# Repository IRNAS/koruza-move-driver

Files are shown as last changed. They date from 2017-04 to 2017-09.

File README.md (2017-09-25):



# Koruza move driver

The Koruza driver is an additional board to [Koruza CM board][link1_koruza_compute_module_repo]. The Koruza move driver is just a simple board dedicated to only one true real-time task - moving the stepper motors.

The main and only MCU on the board is the one and only ATmega328P, which is Arduino compatible. The MCU tasks are: driving the stepper motors, reading the switches and encoders, and communicating with the main board. For driving motors, there is one high-current Darlington transistor array. On the board back, at the end of the motor shafts two magnetic encoders are positioned. Two encoders are TLV493D from Infineon.

For more information about the design of the koruza move driver please see the [Schematics and PCB design files in PDF format][link3_pdf].
The firmware for the koruza move driver board is in the [firmware repository][link2_fw_repo].

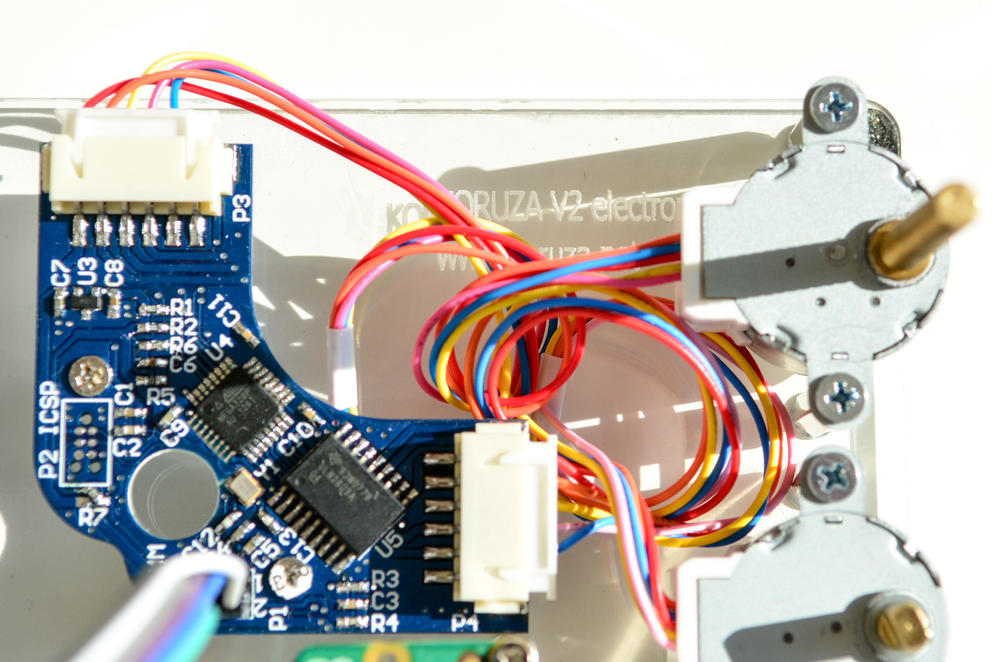
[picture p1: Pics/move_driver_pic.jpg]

---

## Licensing

KORUZA Pro Hardware with documentation, including Koruza move driver, is licensed under [CERN OHL v.1.2. license](https://www.ohwr.org/licenses/cern-ohl/license_versions/v1.2).

What this means is that you can use this hardware and documentation without paying a royalty and knowing that you'll be able to use your version forever. You are also free to make changes but if you share these changes then you have to do so on the same conditions that you enjoy.

KORUZA, KORUZA Pro and IRNAS are all names and marks of Institute IRNAS Rače. You may use these names and terms only to attribute the appropriate entity as required by the Open Licence referred to above. You may not use them in any other way and in particular you may not use them to imply endorsement or authorization of any hardware that you design, make or sell.

[link1_koruza_compute_module_repo]: https://github.com/IRNAS/koruza-compute-module
[link2_fw_repo]: https://github.com/IRNAS/Koruza-Move-Driver-Firmware
[link3_pdf]: https://github.com/IRNAS/koruza-move-driver/blob/master/Koruza%20move%20driver/Project%20Outputs%20for%20PCB_Project_KoruzaMoveDriver/koruza-move-driver-PCB.pdf

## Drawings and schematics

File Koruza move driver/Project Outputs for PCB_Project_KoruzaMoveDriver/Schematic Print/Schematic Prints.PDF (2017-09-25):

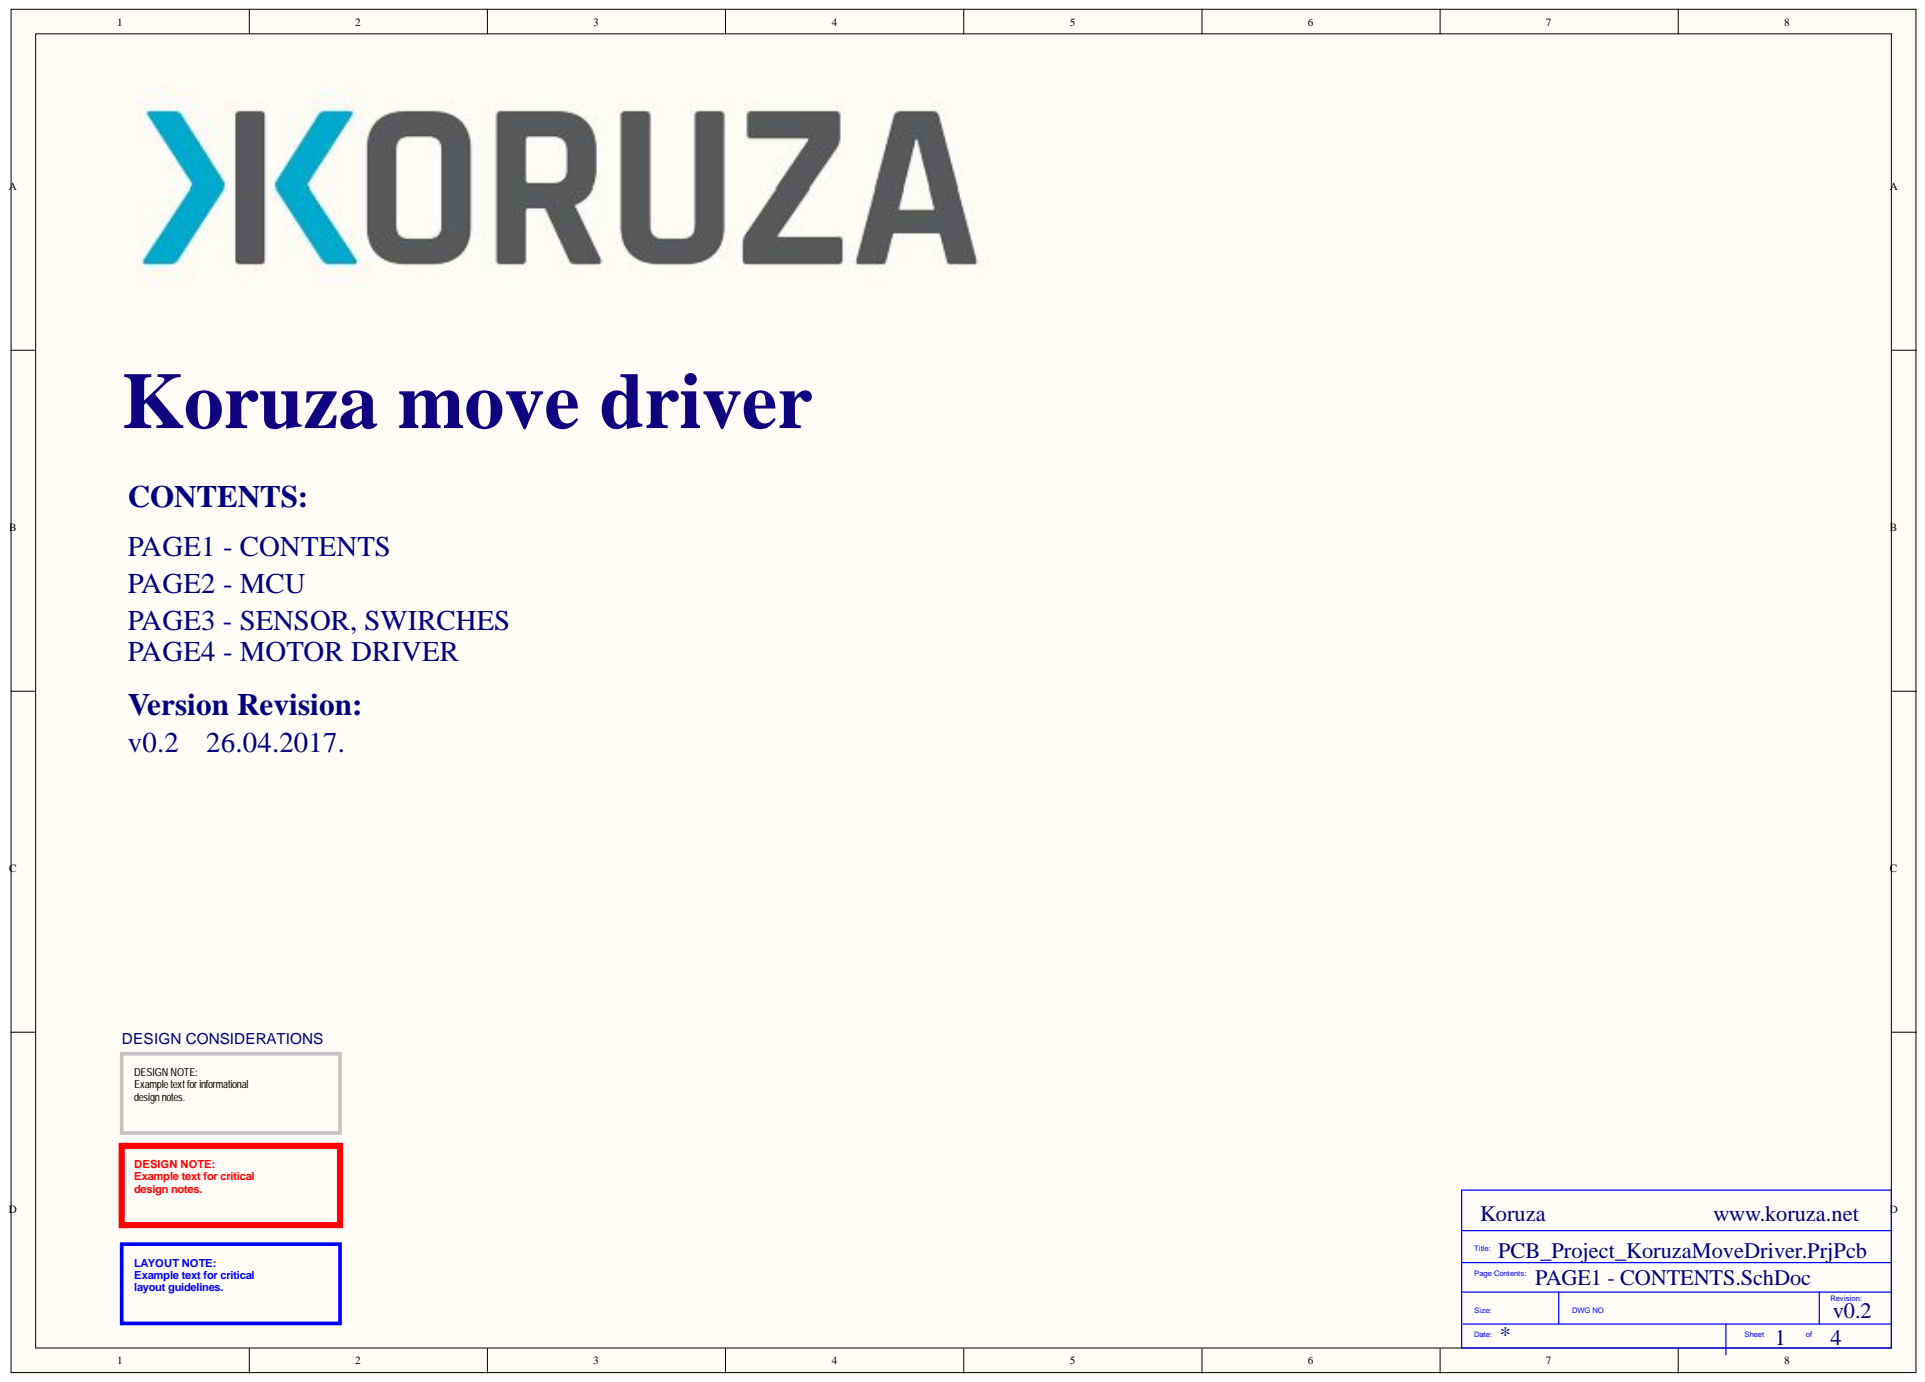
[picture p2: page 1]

DESIGN NOTE:
Example text for informational
design notes.

Example text for critical

LAYOUT NOTE:
layout guidelines.

Size: | DWG NO | Revision: v0.2

* Date: | 1 4 Sheet of

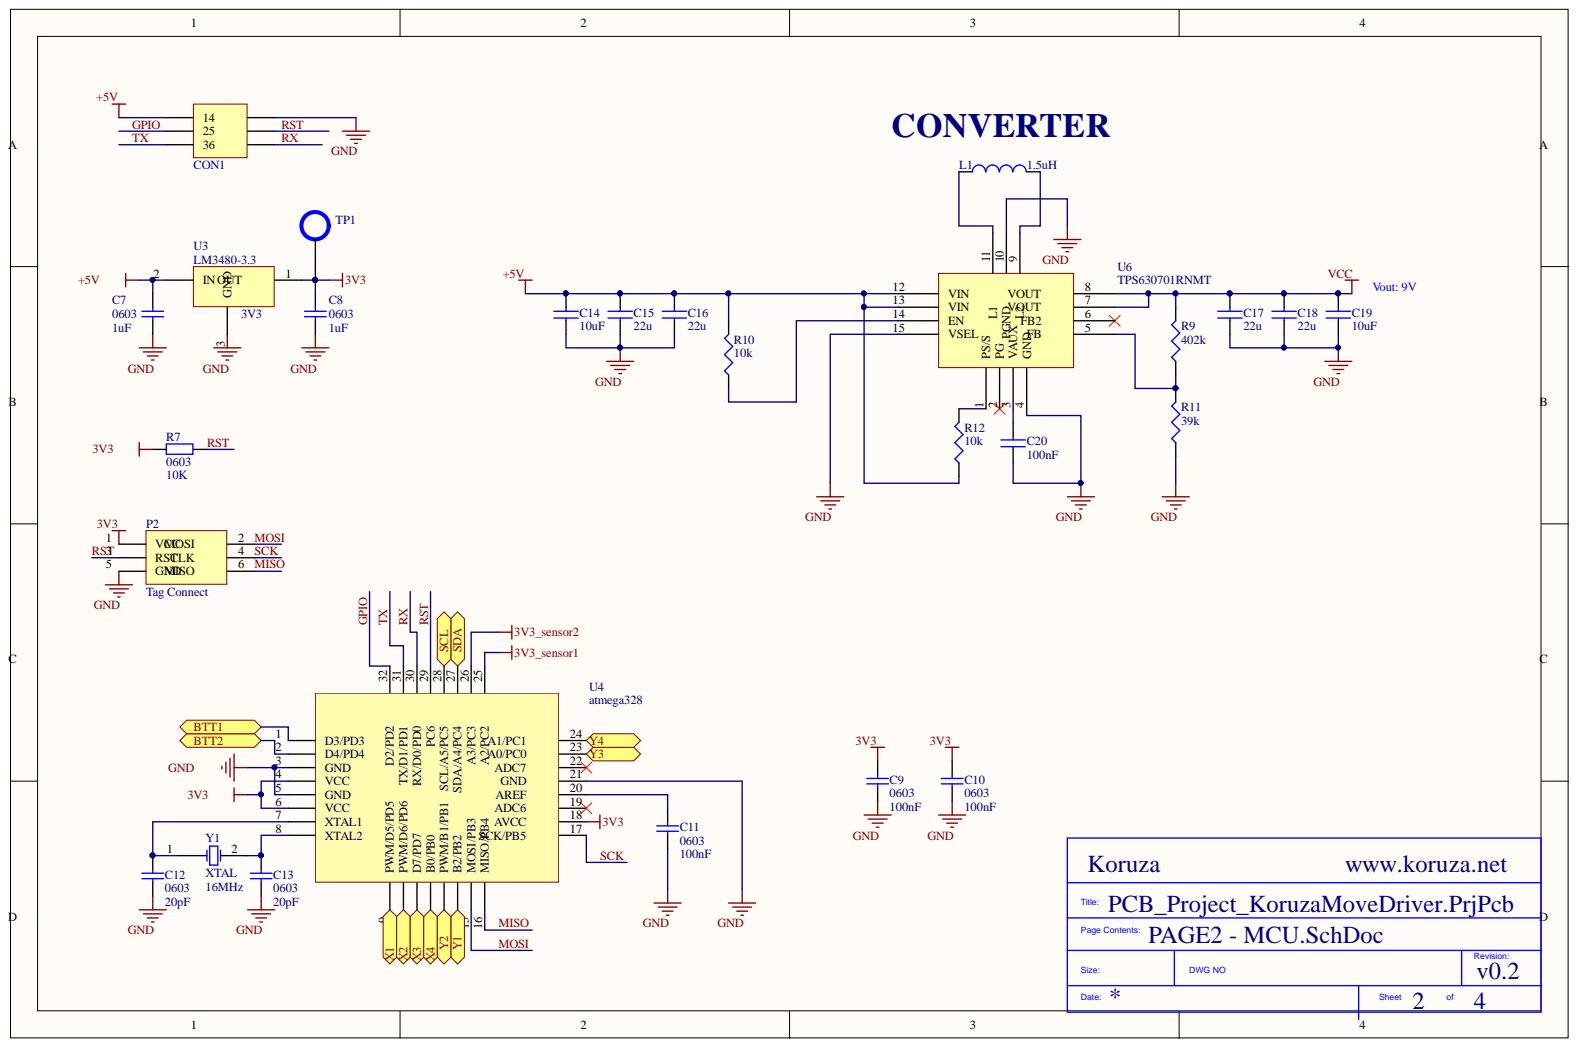
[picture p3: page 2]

GND 4 FB 5 FB2 6 VOUT 7 VOUT 8

A2/PC2 25 A3/PC3 26 SDA/A4/PC4 27 SCL/A5/PC5 28 PC6 29 RX/D0/PD0 30 TX/D1/PD1 31 D2/PD2 32

MISO/PB4 16 SCK/PB5 17 AVCC 18 ADC6 19 AREF 20 GND 21 ADC7 22 A0/PC0 23 A1/PC1 24

D4/PD4 2
GND 3

GND 5

Size: | DWG NO | Revision: v0.2

* Date: | 2 4 Sheet of

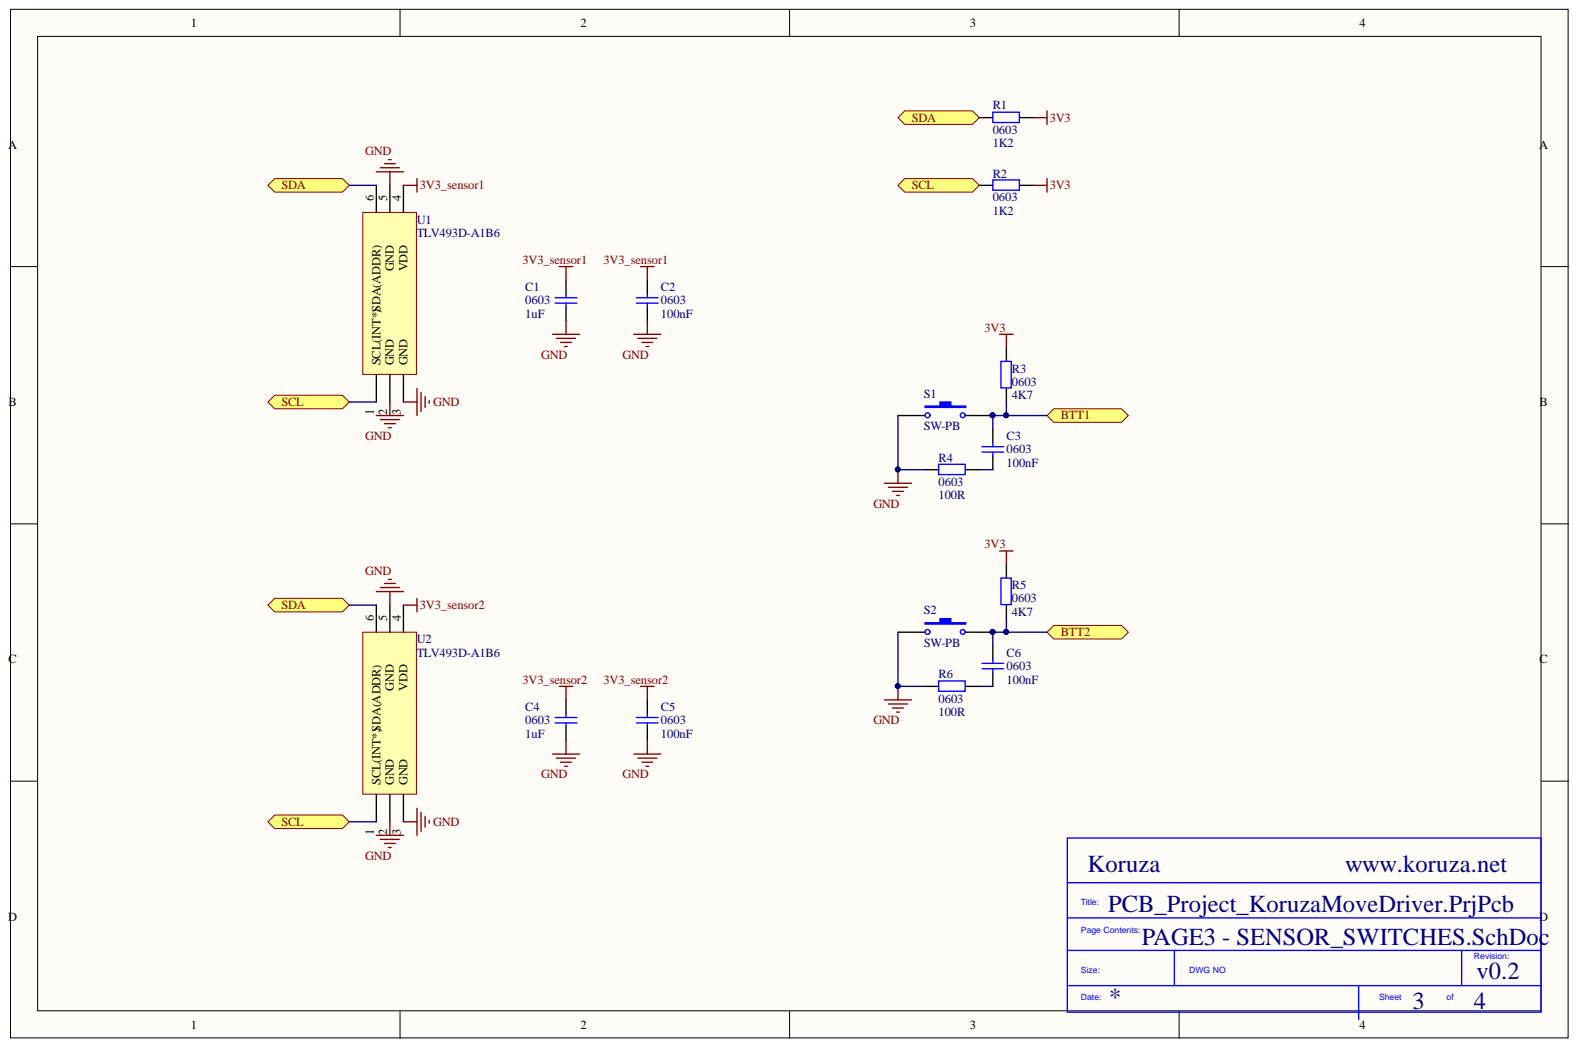
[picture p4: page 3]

GND 3 VDD 4 GND 5 SDA(ADDR) 6

Size: | DWG NO | Revision: v0.2

* Date: | 3 4 Sheet of

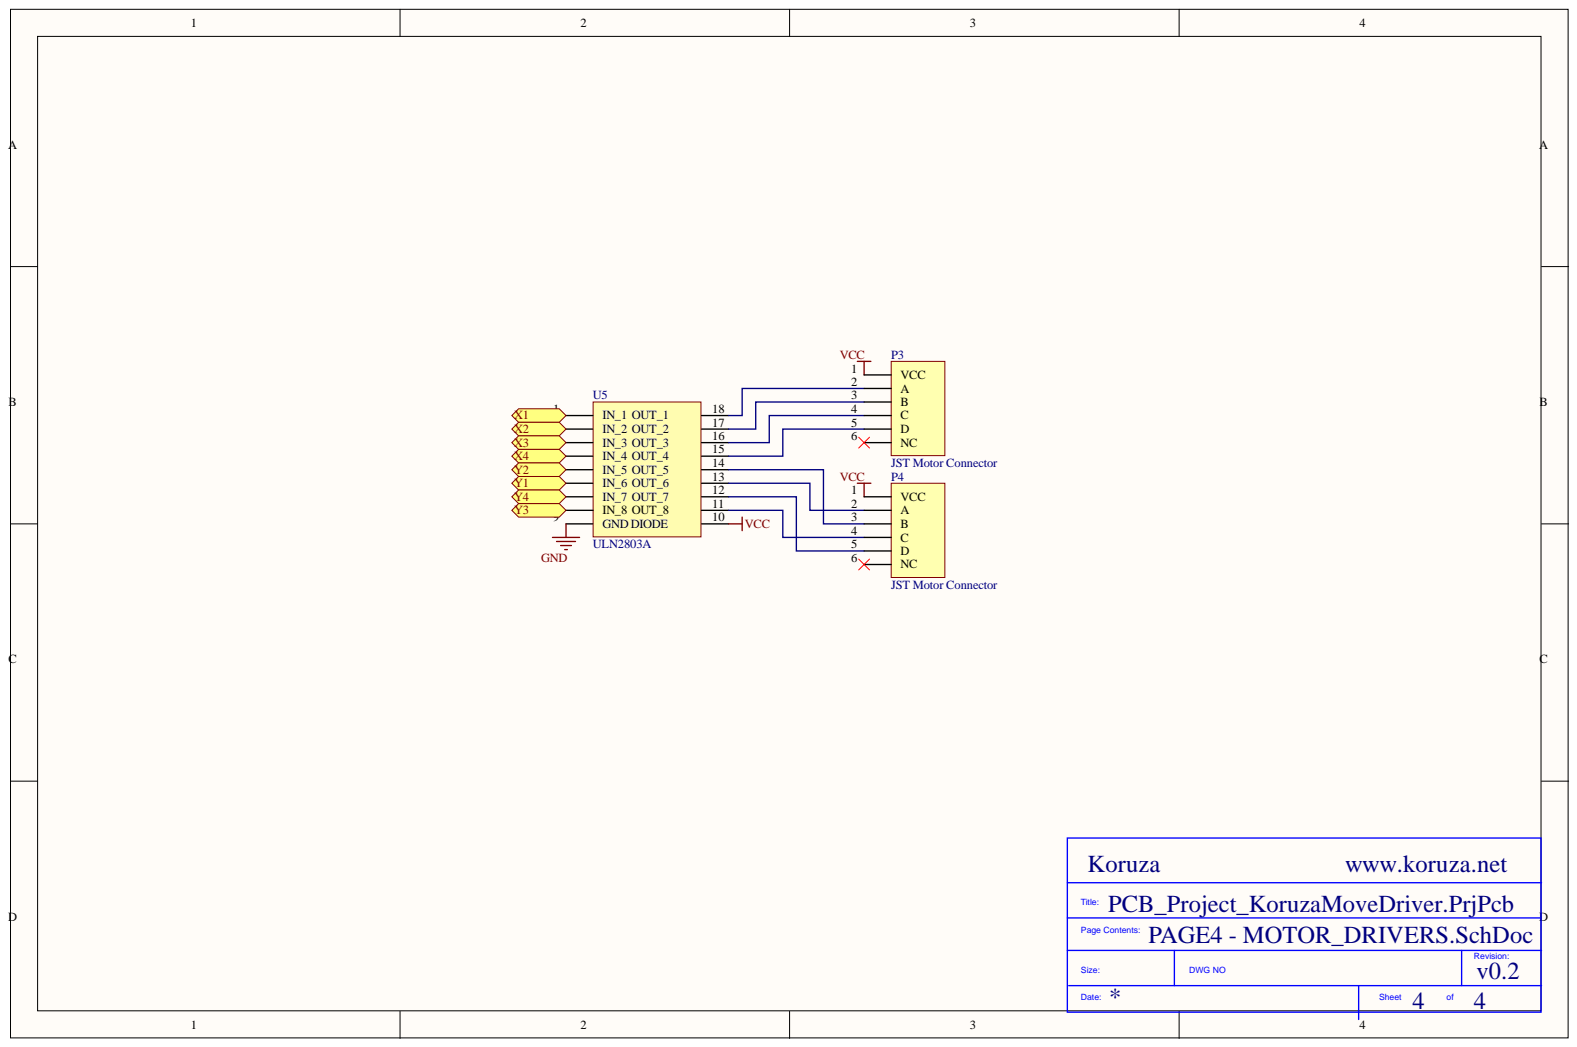
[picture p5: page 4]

Size: | DWG NO | Revision: v0.2

Date: | Sheet of

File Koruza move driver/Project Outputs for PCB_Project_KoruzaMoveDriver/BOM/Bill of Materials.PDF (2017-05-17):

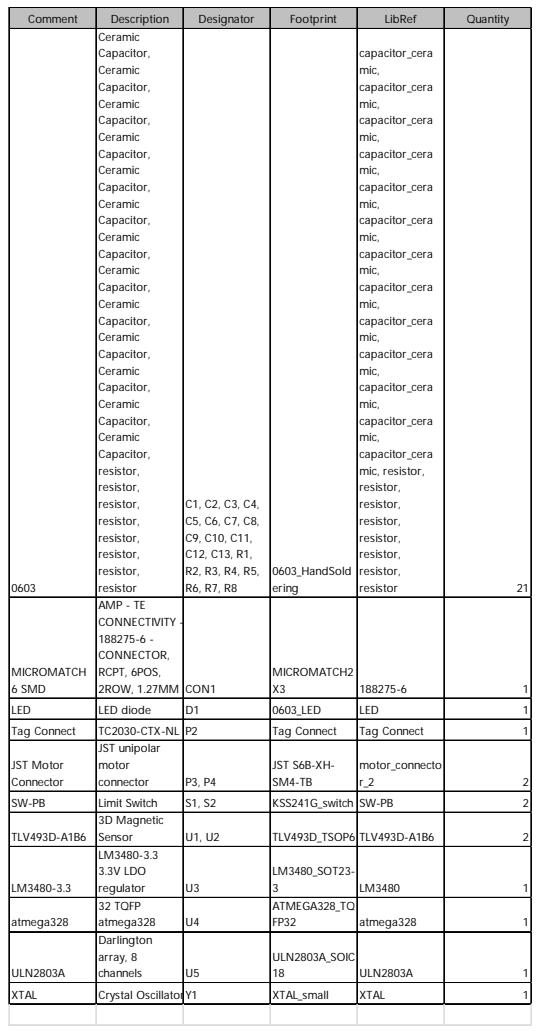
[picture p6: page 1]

MICROMATCH 6 SMD | AMP - TE CONNECTIVITY -188275-6 -CONNECTOR, RCPT, 6POS, 2ROW, 1.27MM | CON1 | MICROMATCH2 X3 | 188275-6 | 1

LED | LED diode | D1 | 0603_LED | LED | 1

Tag Connect | TC2030-CTX-NL | P2 | Tag Connect | Tag Connect | 1
JST Motor Connector | JST unipolar motor connector | P3, P4 | JST S6B-XH-SM4-TB | motor_connecto r_2 | 2

SW-PB | Limit Switch | S1, S2 | KSS241G_switch | SW-PB | 2
TLV493D-A1B6 | 3D Magnetic Sensor | U1, U2 | TLV493D_TSOP6 | TLV493D-A1B6 | 2

LM3480-3.3 | LM3480-3.3 3.3V LDO regulator | U3 | LM3480_SOT23-3 | LM3480 | 1

atmega328 | 32 TQFP atmega328 | U4 | ATMEGA328_TQ FP32 | atmega328 | 1

ULN2803A | Darlington array, 8 channels | U5 | ULN2803A_SOIC 18 | ULN2803A | 1

XTAL | Crystal OscillatorY1 | | XTAL_small | XTAL | 1

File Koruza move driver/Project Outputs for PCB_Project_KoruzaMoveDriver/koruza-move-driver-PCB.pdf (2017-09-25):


DESIGN NOTE:
Example text for informational
design notes.

Example text for critical

LAYOUT NOTE:
layout guidelines.

Size: | DWG NO | Revision: v0.2

* Date: | 1 4 Sheet of


GND 4 FB 5 FB2 6 VOUT 7 VOUT 8

A2/PC2 25 A3/PC3 26 SDA/A4/PC4 27 SCL/A5/PC5 28 PC6 29 RX/D0/PD0 30 TX/D1/PD1 31 D2/PD2 32

MISO/PB4 16 SCK/PB5 17 AVCC 18 ADC6 19 AREF 20 GND 21 ADC7 22 A0/PC0 23 A1/PC1 24

D4/PD4 2
GND 3

GND 5

Size: | DWG NO | Revision: v0.2

* Date: | 2 4 Sheet of


GND 3 VDD 4 GND 5 SDA(ADDR) 6

Size: | DWG NO | Revision: v0.2

* Date: | 3 4 Sheet of


Size: | DWG NO | Revision: v0.2

Date: | Sheet of

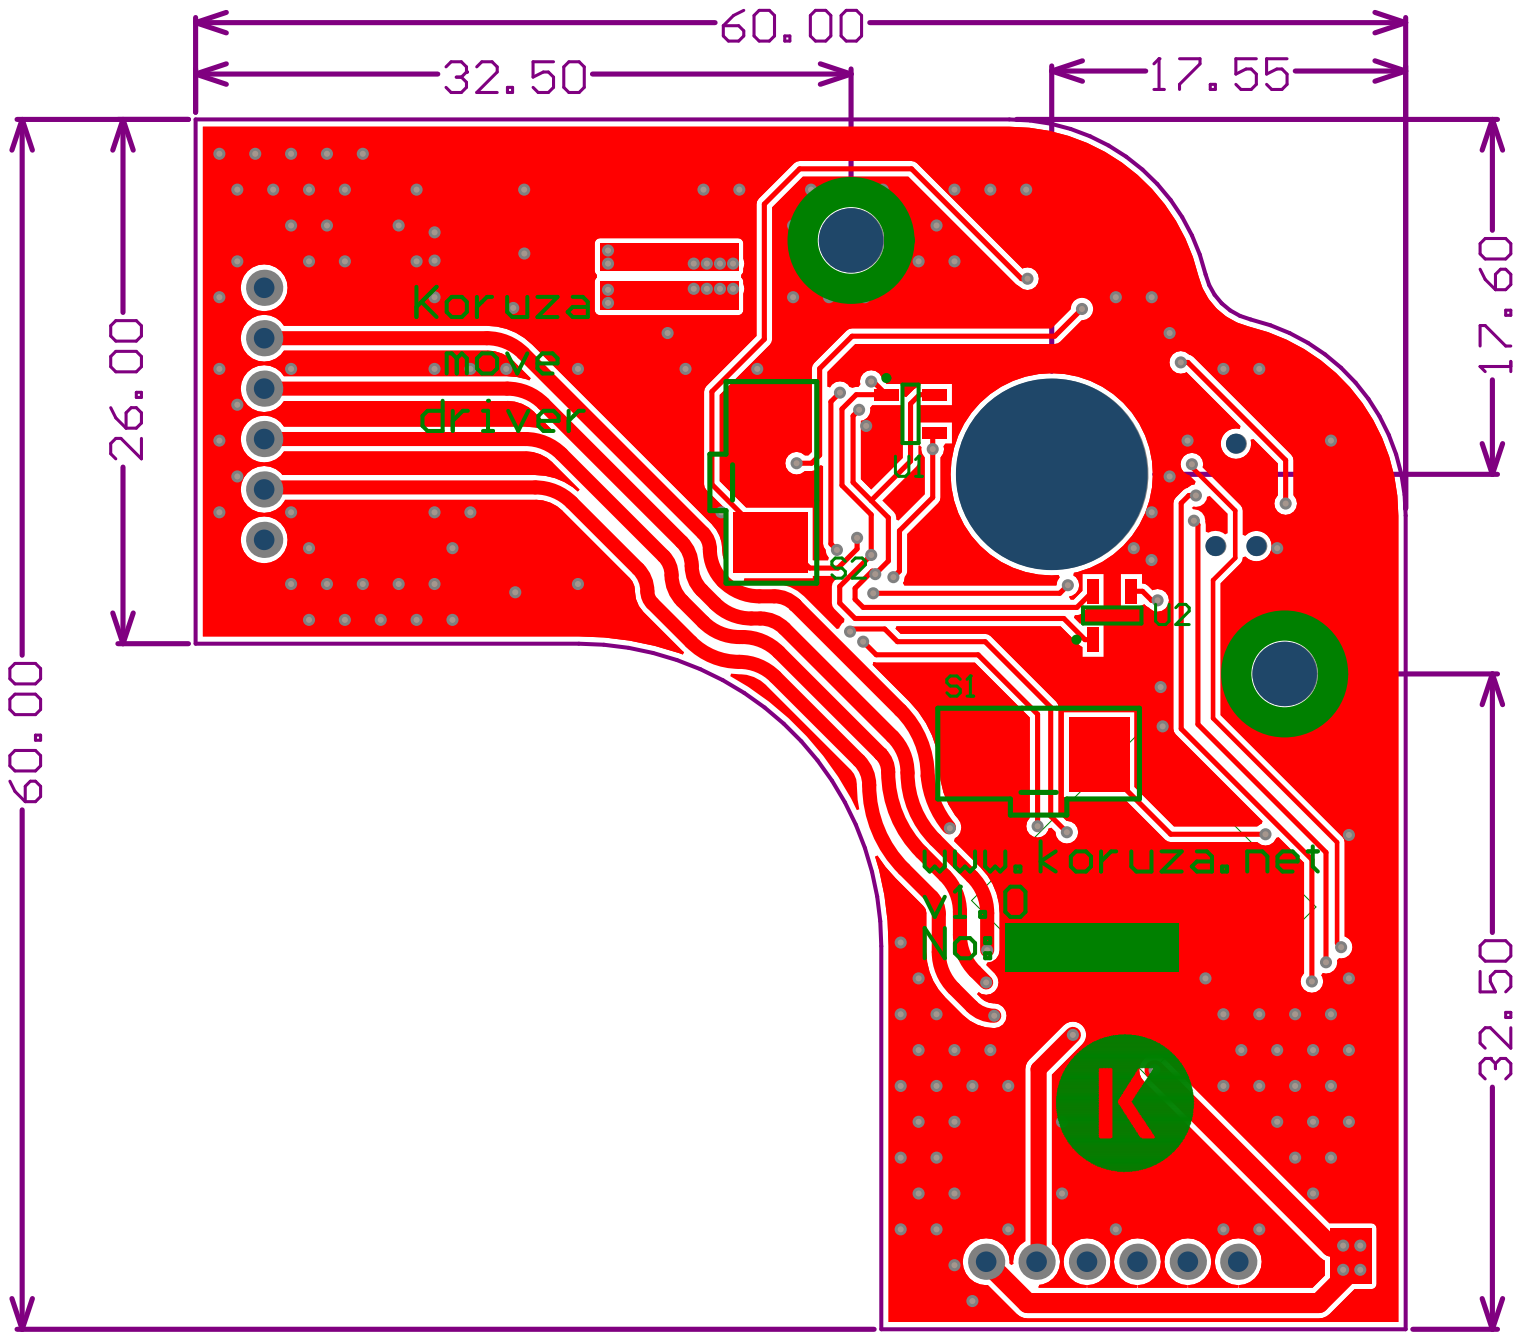
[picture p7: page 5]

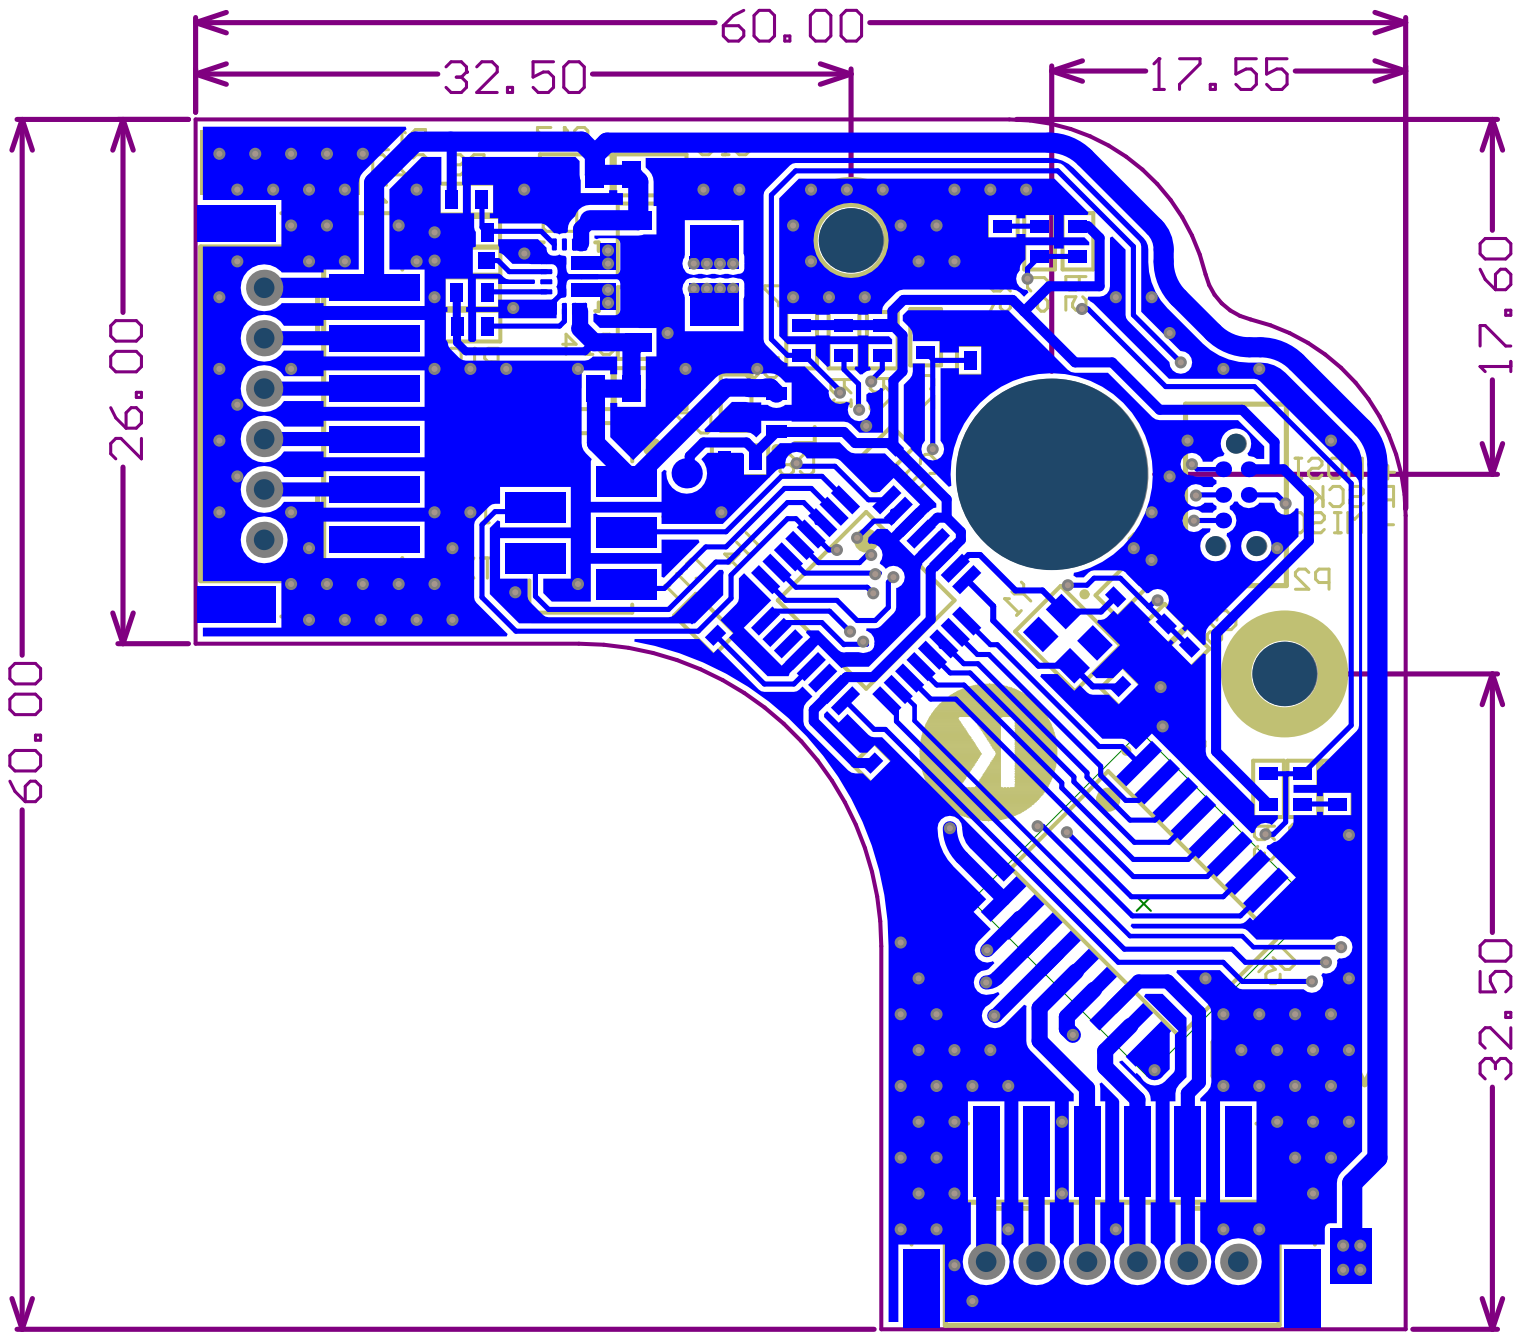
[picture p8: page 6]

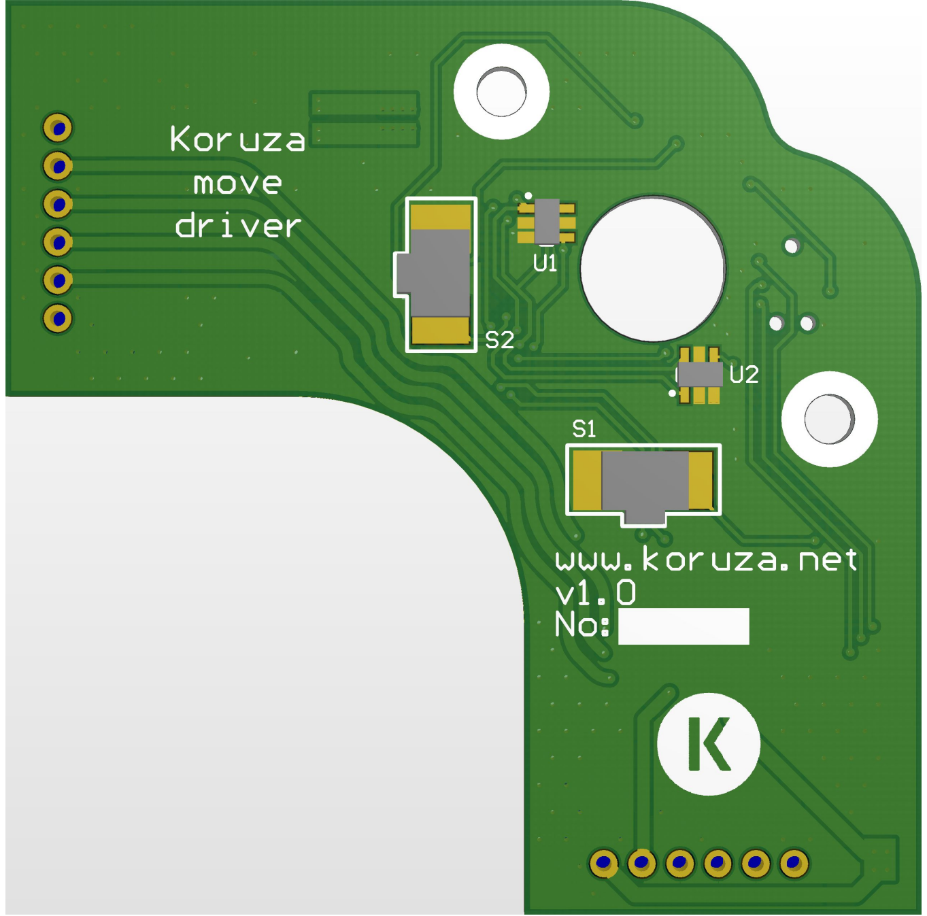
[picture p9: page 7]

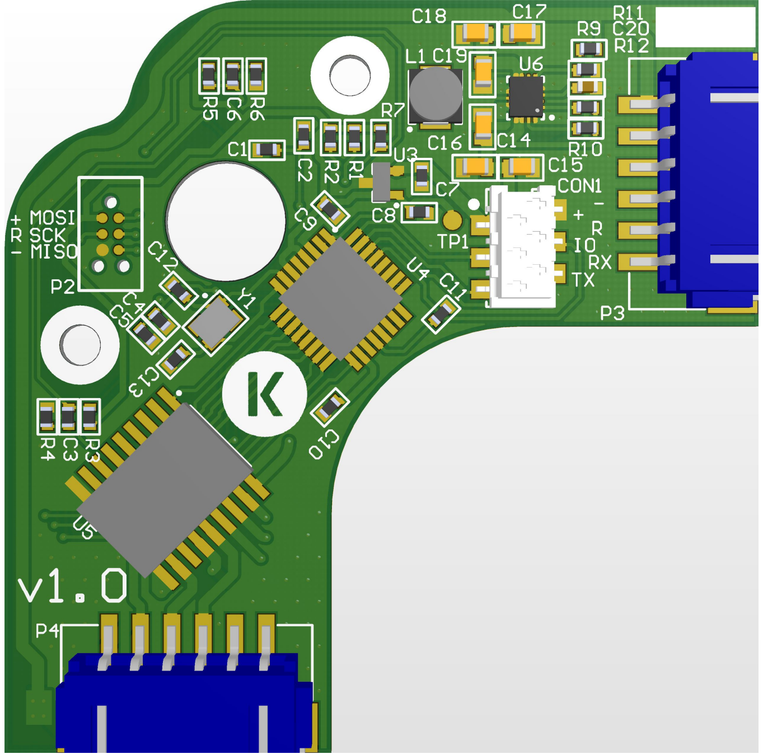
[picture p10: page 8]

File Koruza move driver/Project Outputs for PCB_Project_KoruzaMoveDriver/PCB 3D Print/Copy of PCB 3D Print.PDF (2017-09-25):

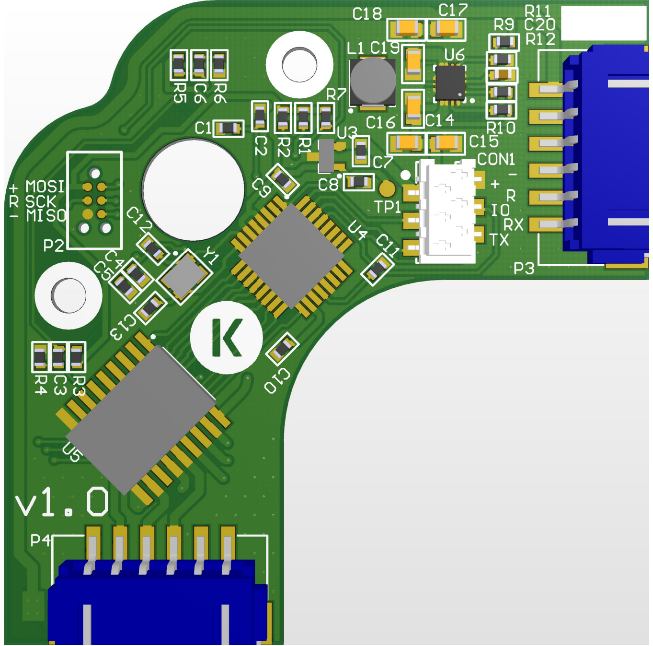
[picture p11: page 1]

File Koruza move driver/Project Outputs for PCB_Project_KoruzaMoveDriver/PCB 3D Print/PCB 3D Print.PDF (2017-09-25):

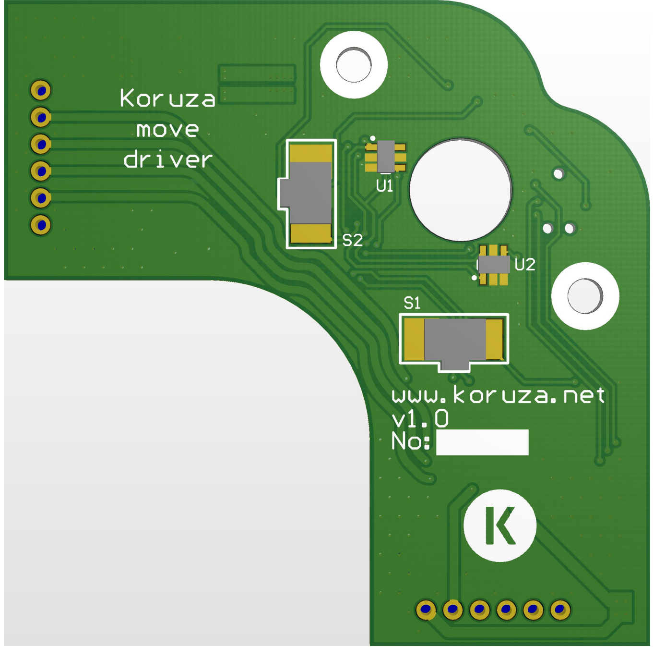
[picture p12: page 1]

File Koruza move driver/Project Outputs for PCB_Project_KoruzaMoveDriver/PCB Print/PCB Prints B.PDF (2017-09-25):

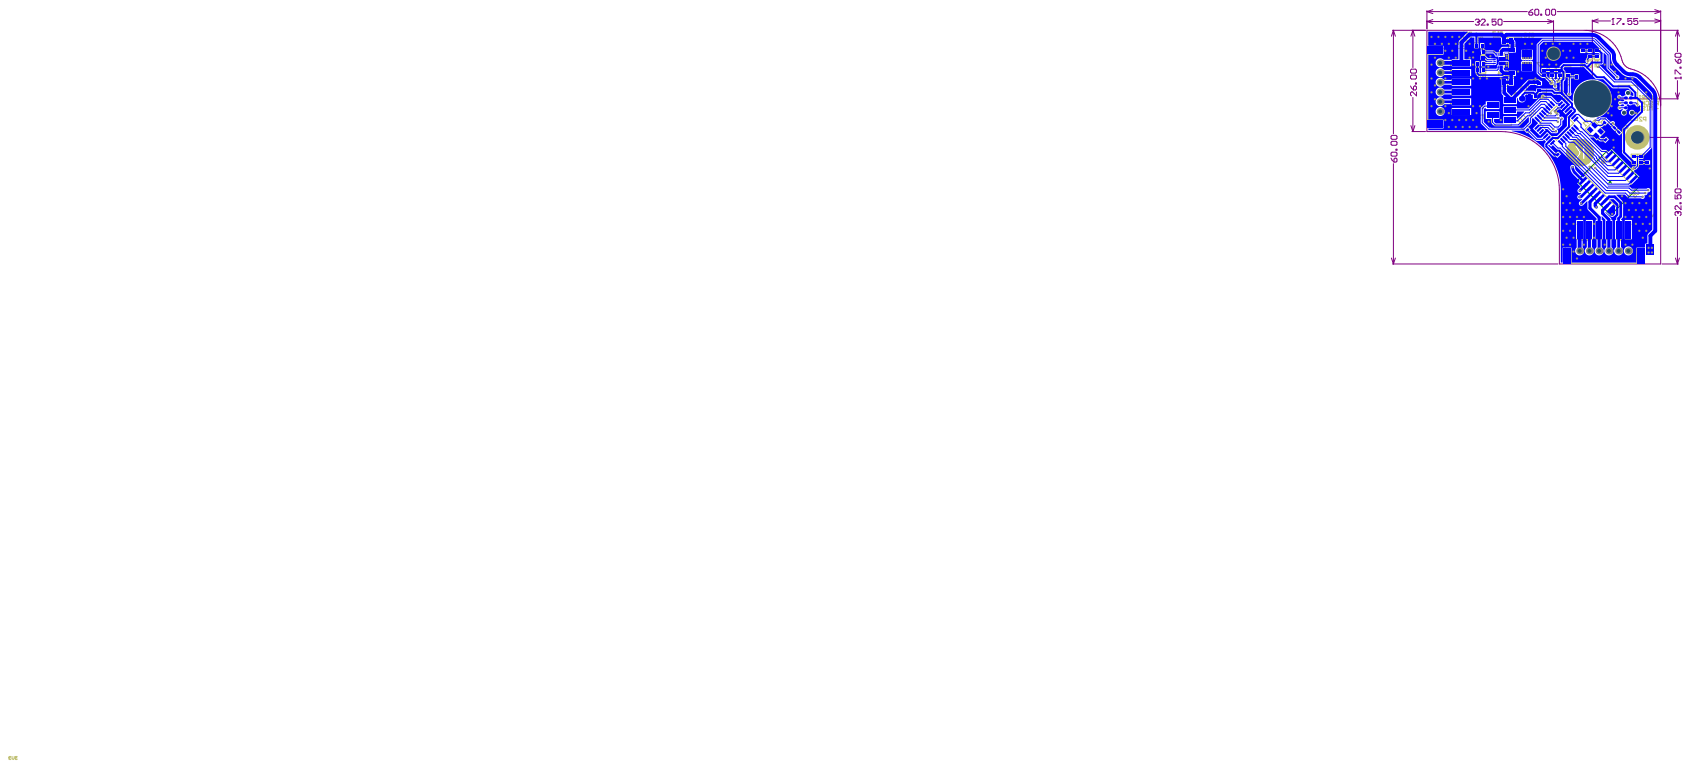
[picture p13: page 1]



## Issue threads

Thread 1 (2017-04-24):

Communication and power connector

VojislavM, 2017-04-24:
Change the communication and power connector from standard 2.54 mm pitch header to 6 pin micromatch SMD connector.

Closed 2017-04-26.

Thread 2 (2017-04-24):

Programming connector

VojislavM, 2017-04-24:
Check the pin order for programming connector. Programator is Atmel ICE basic and connector is TAG connector. Documentation for the connector is in the [repo](https://github.com/IRNAS/koruza-move-driver/tree/master/Docs/Datasheet/prog%20connect) .

Closed 2017-04-26.

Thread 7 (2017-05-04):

LED GPIO problem

VojislavM, 2017-05-04:
Possible problem is that LED on PIN23/ADC7 is not going to work because that pin is only connected to the ADC inside the chip (only in SMD package of atmefa328p). This is also the case with ADC6, and those two pins were only available for the LED....

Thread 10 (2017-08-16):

Power for motors

VojislavM, 2017-08-16:
Input power 5V instede of 9V
step up form 5 to  9 V

VojislavM, 2017-08-17:
boost form 5V
http://uk.farnell.com/microchip/mic2288yd5-tr/voltage-reg-boost-1a-1-2mhz-tsot23/dp/2509929

VojislavM, 2017-08-17:
test this solution

VojislavM, 2017-09-25:
same as on PiRA, [TSP_backboost](https://github.com/IRNAS/IoT-battery-pack/tree/modular/IoT-Battery-pack-PCB/IRNAS_TSP_buckboost).

SloMusti, 2017-10-07:
Motor movement tested with new power supply, correct operation observed.

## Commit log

2017-04-24 init commit
    [Header Vertical 2_54mm.STEP, JST B5B-XH-A.STEP, PCB - encoder v2.STEP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]
2017-04-24 add design files
    [PAGE1 - CONTENTS.SchDoc, PAGE2 - MCU.SchDoc, PAGE3 - SENSOR_SWITCHES.SchDoc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]
2017-04-25 pcb lib update
    [PcbLib1.PcbLib, koruza-move-driver-PCB.PcbDoc]
2017-04-26 PCB update Fixes #1 Fixes #2 Fixes #3
    [PAGE2 - MCU.SchDoc, PCB_Project_KoruzaMoveDriver.PrjPcb, PcbLib1.PcbLib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]
2017-04-26 pcb update Fixes #4 Fixes #5 Fixes #6
    [koruza-move-driver-PCB.PcbDoc]
2017-04-26 gerver update
    [koruza-move-driver-PCB.DRL, koruza-move-driver-PCB.GBL, koruza-move-driver-PCB.GBO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]
2017-04-26 pdf update
    [PAGE1 - CONTENTS.SchDoc]
2017-04-27 gerber update
    [PAGE2 - MCU.SchDoc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]
2017-05-17 v0.2 done
    [PAGE1 - CONTENTS.SchDoc, PCB_Project_KoruzaMoveDriver.PrjPcb]
2017-09-07 remove docs
    [Header Vertical 2_54mm.STEP, JST B5B-XH-A.STEP, PCB - encoder v2.STEP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]
2017-09-25 add new version 1.0
    [PAGE2 - MCU.SchDoc, PAGE4 - MOTOR_DRIVERS.SchDoc, PcbLib1.PcbLib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]
